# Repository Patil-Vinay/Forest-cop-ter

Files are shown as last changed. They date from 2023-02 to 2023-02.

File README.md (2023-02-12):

# Forestcopter

The main objective of creating an application-based drone is to introduce the tech world and tech community to head towards advantageous approach of saving a life with an Unmanned Aerial Vehicles (UAVs), conserve time and a huge involvement of precise automated machines that can be created with the fundamental knowledge of computer science, electrical/electronic, and mechanics.

Deployed a drone into the forest sector so that it can come handy for the Forest Rescue Department. Thus following were the features that were customized into it:

- Camera Surveillance using Raspberry Pi
- Calling system using GSM Module
- Forest Fire prediction system
- GPS Location
- First Aid Box that opens through servo motor
- All these applications could be observed or controlled through GUI APP.

## Graphical Abstract
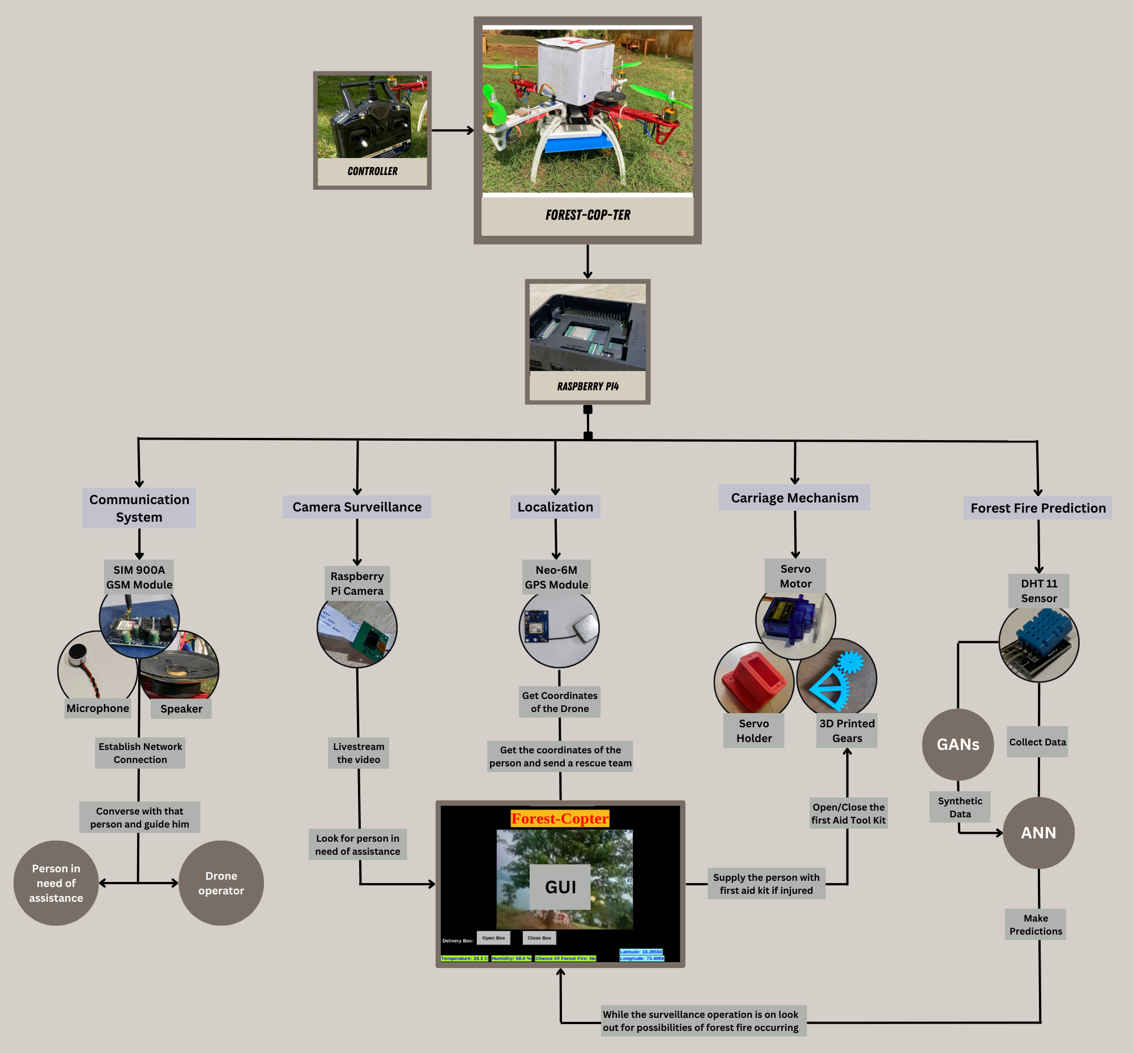
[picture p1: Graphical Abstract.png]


## Project Preview
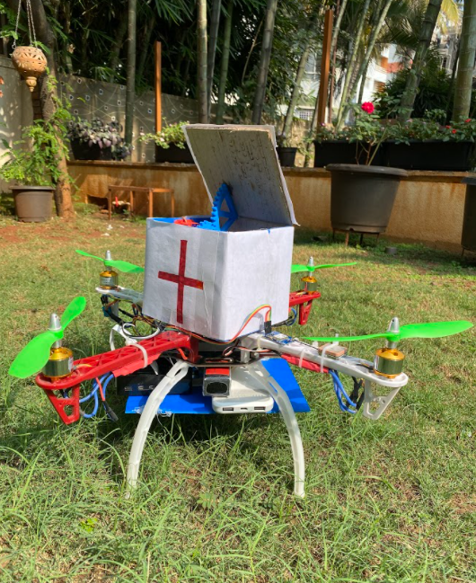
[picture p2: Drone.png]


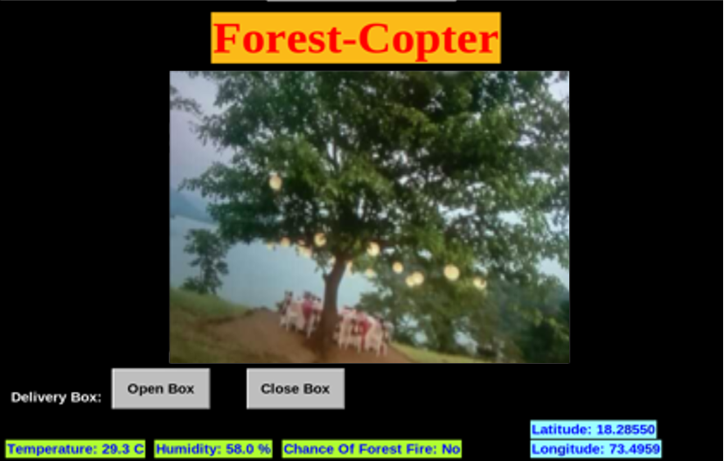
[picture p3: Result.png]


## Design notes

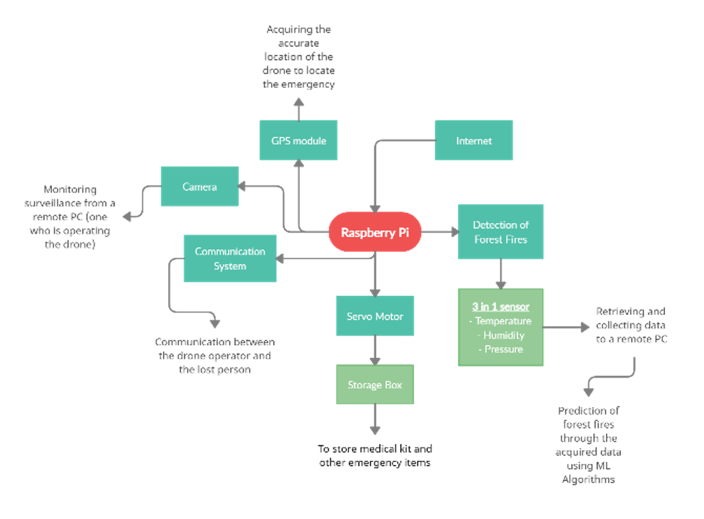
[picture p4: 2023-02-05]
Block Diagram.png

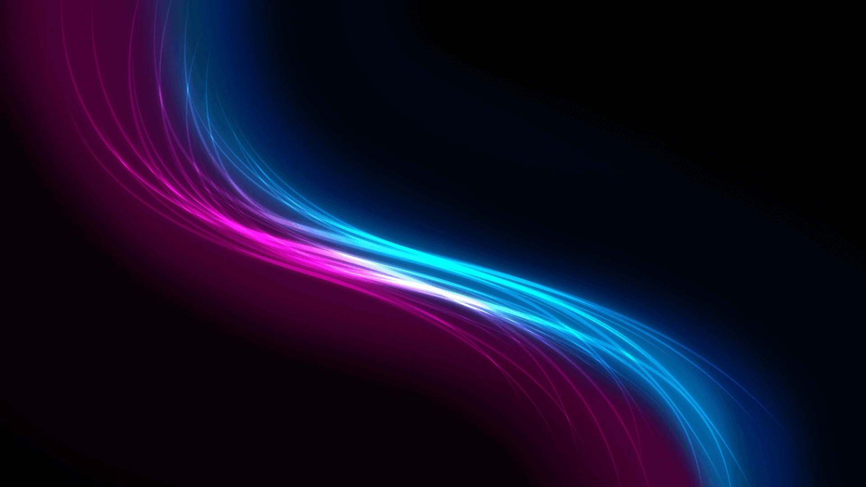
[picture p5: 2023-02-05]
bg.gif

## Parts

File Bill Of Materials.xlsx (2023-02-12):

Designator | Component | Number | Cost per unit - USD | Total cost - USD | Source of materials | Material type
P01 | RaspberryPi 4 | 1 | 70 | 70 | https://robu.in/ (https://robu.in/product/raspberry-pi-4-model-b-with-4-gb-ram/) | Semiconductor
P02 | Orange 5200mAh Battery | 1 | 42 | 42 | https://robu.in/ (https://robu.in/product/orange-5200mah-3s-40c80c-lithium-polymer-battery-pack-lipo/) | Non-specific
P03 | Neo6m GPS Module | 1 | 3.71 | 3.71 | https://robu.in/ (https://robu.in/product/ublox-neo-6m-gps-module/) | Semiconductor
P04 | RaspberryPi Camera | 1 | 25.44 | 25.44 | https://robu.in/ (https://robu.in/product/raspberry-pi-camera-v2/) | Semiconductor
P05 | GSM Sim900A | 1 | 13.32 | 13.32 | https://www.amazon.in/ (https://www.amazon.in/Electronics-SIM900A-Modem-Antenna-Module/dp/B07145FD3J) | Semiconductor
P06 | TowerPro Micro Servo SG90 | 1 | 1.93 | 1.93 | https://robu.in/ | Polymer
P07 | DHT11 Temperature Sensor | 1 | 1.2 | 1.2 | https://robu.in/ (https://robu.in/product/dht11-temperature-and-humidity-sensor-module-with-led/) | Semiconductor
P08 | Microphone | 1 | 0.59 | 0.59 | https://robu.in/ (https://robu.in/product/microphone-97mm-pack-of-3/) | Semiconductor
P09 | Speaker | 1 | 0.55 | 0.55 | https://www.electronicscomp.com/ (https://www.electronicscomp.com/8-ohm-speaker-0.5-watt) | Semiconductor
P10 | DJI F450 Drone Frame | 1 | 20.84 | 20.84 | https://www.amazon.in/ (https://www.amazon.in/Invento-Quadcopter-MultiCopter-Airframe-Landing/dp/B07D42SS88) | Polymer
P11 | Simonk 30A ESC | 4 | 4.85 | 19.4 | https://robu.in/ (https://robu.in/product/30a-bldc-esc-electronic-speed-controller/) | Semiconductor
P12 | 1000KV Brushless Motor | 4 | 3.64 | 14.56 | https://robu.in/ (https://robu.in/product/a2212-10t-13t-1000kv-brushless-motor-without-soldered-connector/) | Metal
P13 | 8x4.5” Propeller | 4 | 1.2 | 4.8 | https://robu.in/ (https://robu.in/product/orange-hd-propellers-80458x4-5-abs-1cw1ccw-1pair-green/) | Polymer
P14 | KK2.1 Flight Controller | 1 | 50.9 | 50.9 | https://robu.in/ (https://robu.in/product/kk2-1-5-multi-rotor-lcd-flight-control-board-with-6050mpu-and-atmel-644pa/) | Semiconductor
P15 | Flysky 6CH Controller | 1 | 30.28 | 30.28 | https://robu.in/ (https://robu.in/product/ct6b-flysky-2-4ghz-6ch-transmitter-wfs-r6b-receiver-mode-2/) | Semiconductor
P16 | PLA | 1 | 9.69 | 9.69 | https://robu.in/ (https://robu.in/product/orange-epla-1-75mm-3d-printing-filament-1kg-white/) | Polymer
P17 | USB to Type C cable | 1 | 1.72 | 1.72 | https://robu.in/ (https://robu.in/product/5v-3a-usb-to-type-c-cable-with-on-off-switch-power-control-for-raspberry-pi-4b-1-meters-black/) | Non-specific
P18 | Dual USB Output | 1 | 2.42 | 2.42 | https://robu.in/ (https://robu.in/product/dual-usb-output-9v-12v-24v-36v-car-charger-switch-5v-dc-dc-power-supply-module-3a-buck-regulator/) | Semiconductor
P19 | Pole Wire Connector Terminal Block | 1 | 1.56 | 1.56 | https://robu.in/ (https://robu.in/product/pct-spl-62-0-08-2-5mm-62-pole-wire-connector-terminal-block-with-spring-lock-lever-for-cable-connection/) | Semiconductor
P20 | Jumper Wires | 1 | 1.09 | 1.09 | https://robu.in/ | Semiconductor
P21 | Small Breadboard | 1 | 0.35 | 0.35 | https://robu.in/ (https://robu.in/product/170-pts-mini-breadboard-syb-170-white/) | Semiconductor
P22 | Cardboard | 1 | 0.61 | 0.61 | Local Store | Non-specific
P23 | Sheet metal | 1 | 1.21 | 1.21 | Local Store | Metal
P24 | Spacers | 1 | 0.12 | 0.12 | Local Store | Polymer

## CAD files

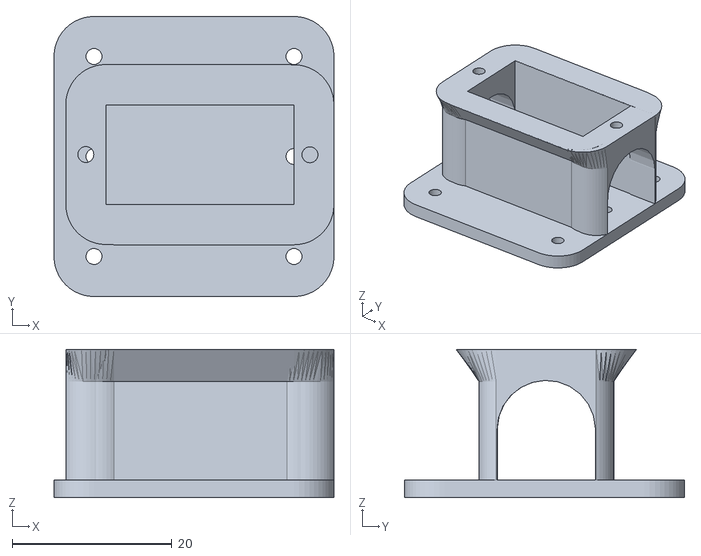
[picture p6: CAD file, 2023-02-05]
Servo_Holder.stl
35.0 x 35.0 x 18.5

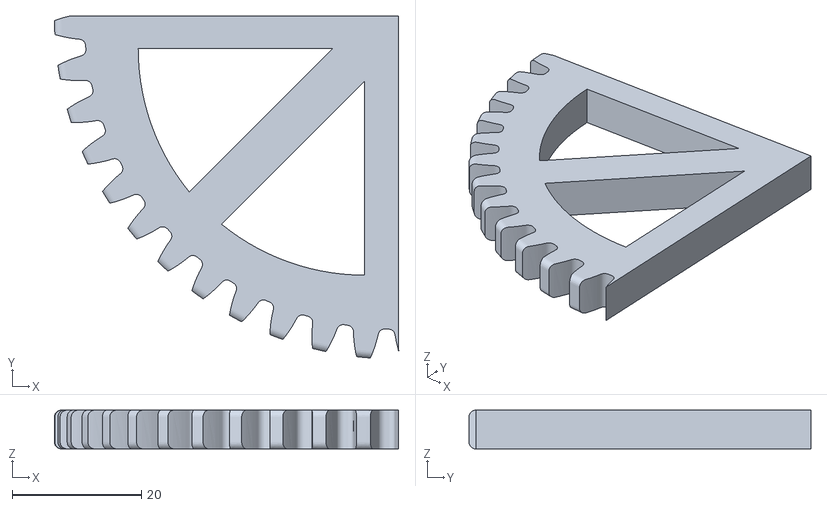
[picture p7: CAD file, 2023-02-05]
gear_mech_mount.stl
53.2 x 52.9 x 6.00

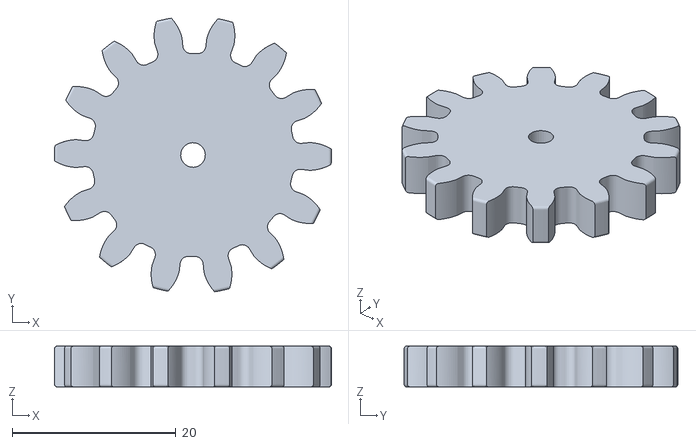
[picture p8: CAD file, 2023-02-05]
gear_mechanism.stl
33.8 x 33.4 x 5.00

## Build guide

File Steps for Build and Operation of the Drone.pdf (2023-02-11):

Steps for Build and Operation of the Drone:

A) Drone Assembly:
1. Mount 1000KV Brushless motors to the F450 quadcopter frame using M3 screws.
2. Solder the ESC and power wire to the power pads and insert the power wire in the Pole Wire Terminal block, making sure to connect blue for positive or negative.
3. Mount the KK2.1 flight controller on the top of the quadcopter frame.
4. Connect the ESCs to the motors and connect the signal cable from the ESCs to the flight controller (white wire is the signal, red is power, and black is ground).
5. Connect the Flysky receiver to the flight controller (signal to signal, +5V to +5V, and ground to ground).
6. Connect the receiver channels to the flight controller, starting with Channel 1 at the topmost pin on the left side.
7. Assemble the top and bottom boards to the arms and legs of the quadcopter frame.
8. Calibrate the Flight controller and ESC.
9. Connect the propellers and test the drone in an open environment.
10. Mount all components, such as the Raspberry Pi, sensors, and carriage mechanism, on the drone.
11. Create a box or make a box from cardboard and cut a sheet metal of 12x12cm dimension and fix it with the base of the box.
12. Attach the box to the top plate of the drone with spacers.
B) Interfacing Raspberry Pi with required components:
1. Connect the Pole Wire Terminal block output to the input of the Dual USB Output module.
2. Use a USB to type C cable to connect the Dual USB Output module to the USB port of the Raspberry Pi 4 to power it.
3. Connect the Raspberry Pi camera to the camera module port of the Raspberry Pi 4.
4. Connect the Vcc pin of the Neo6M GPS module to 5V of the Raspberry Pi 4, the Ground pin of the GPS module to Ground of the Raspberry Pi 4, and the Tx pin of the GPS module to the Rx pin (GPIO 27) of the Raspberry Pi 4.
5. Connect the Vcc pin of the DHT11 Temperature sensor to 3.3V of the Raspberry Pi 4, the Ground pin of the Temperature sensor to Ground of the Raspberry Pi 4, and the data pin of the temperature sensor to GPIO 4 of the Raspberry Pi 4.
6. Connect the Vcc pin of the TowerPro Micro Servo SG90 Motor to 5V of the Raspberry Pi 4, the Ground pin of the servo motor to Ground of the Raspberry Pi 4, and the signal pin of the servo motor to GPIO 18 of the Raspberry Pi 4.
7. Connect the Vcc pin of the GSMSim900A module to 5V of the Raspberry Pi 4, the Ground pin of the GSM module to Ground of the Raspberry Pi 4, and the Rx pin of the GSM module to the Tx pin (GPIO 14) of the Raspberry Pi 4 and the Tx pins of the GSM module to the Rx pin (GPIO 15) of the Raspberry Pi 4.
8. Connect the microphone and speaker to the ports on the GSM module, with the positive wire of the microphone connecting to the "mic_p" port and the negative wire connecting to the "mic_n" port, and the positive wire of the speaker connecting to the "spk_p" port and the negative wire connecting to the "spk_n" port.

C) Generate networks :
1. Load on your Google Drive the notebook files: SyntheticData.ipynb , forestfire_prediction.py.
2. Load on your Google Drive forestfires.csv dataset to be used with the SyntheticData.ipynb file in order to generate the synthetic data.
3. Open the file SyntheticData.ipynb with Google Colaboratory, choose runtime session from the Menu and execute.
4. Load on your Google Drive the file generated from step 3 or you can load the forestfire_augmented.csv dataset to be used with forestfire_prediction.py to train the ANN model and make predictions.
5. Repeat step 3 with forestfire_prediction.py, the output model files will be saved in the same directory of the notebook file.
D) Flysky Transmitter and Receiver Pairing

If the Flysky receiver LED is blinking, this means that the ESC is not paired with the transmitter. To pair the two devices, follow these steps:

1. Disconnect all connections from the Flysky receiver.
2. Connect one of the ESCs to the receiver.
3. Power the ESCs by connecting the battery (P02) to the power cable of the frame.
4. Connect the ESC cable that will go to the flight controller to Channel 1 (CH1) of the receiver.
5. Short the signal and ground pins of the receiver at the BAT channel. If the receiver is not paired, the LED on the receiver will blink continuously.
6. Set the trim levels of the transmitter to the middle position.
7. Press and hold the bind button on the transmitter while turning it on.
8. Observe the receiver LED. If it stops blinking, this means that the transmitter and receiver are paired.
9. Disconnect the power and turn off the Flysky transmitter.
E) Calibrating the Flight Controller
1. Turn on the Flysky transmitter and power the quadcopter by connecting the battery to the power cable.
2. Press the S4 button to access the menu and select the quadcopter X mode by navigating with S2 and S3 buttons.
3. Calibrate the ACC by placing the drone on a flat surface.
4. Perform a Receiver Test in the menu by using S2 and S4 buttons.
5. Set the PI settings according to the table given below.

Instructions for PI Settings:

Parameter | Roll (Aileron) | Pitch (Elevator) | Yaw (Rudder)
P Gain | 75 | 75 | 75
P Limit | 50 | 50 | 20
I Gain | 40 | 40 | 30

I Limit | 20 | 20 | 10
6. Go to the Mode Settings and set the self-level to always.
7. Go to the Miscellaneous Settings and set the Alarm 1/10 volts to 108. This alarm will sound when the supply voltage drops to 10.8V.
F) ESC Calibration
1. Turn on the Flysky transmitter with the throttle stick at minimum and all switches off.
2. Move the throttle stick to maximum.
3. Press and hold S1 and S4 buttons on the flight controller, then connect the battery.
4. Listen for two beep sounds, then move the throttle stick to minimum and listen for a single beep sound.
5. This will complete the ESC calibration.
6. Arm the quadcopter by moving the throttle stick to the bottom left corner.
7. Increase the throttle to verify that the motors are running. Do not attach the propellers.
8. Check the motor rotation and make sure it follows the X configuration.
9. If the rotation is incorrect, interchange the last two wires of the ESC connected to the motor.
G) Calibrating the Raspberry Pi:
1. Write the Raspberry Pi operating system to an SD card using the Raspberry Pi Imager tool.
2. Insert the SD card into the Raspberry Pi and power it on, then follow the on-screen instructions to set it up.
3. Open the terminal and install the required libraries: tkinter, DHT11, PIL, OpenCV, panda, sklearn, keras, pynmea, and smtplib.
4. To use the internet with a GSM module, disable the serial option and connect the Raspberry Pi to the internet via WiFi or Ethernet. Install the PPP software and create a PPP peer configuration file, changing the APN and communication port as needed.
5. Use soft_uart to convert the GPIO pins into Rx and Tx for serial communication.
6. Test the functionality of each sensor/module before running the final file.
7. Install VNC Server on Raspberry Pi and VNC Viewer on the master computer, then connect to the Raspberry Pi remotely using the IP address.
8. Run the "forest-copter" micro python file to see the GUI with information on temperature, humidity, camera feed, GPS module, and forest fire prediction.

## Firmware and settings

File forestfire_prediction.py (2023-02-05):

import RPi.GPIO as GPIO
import dht11
import time
import pandas as pd
from sklearn.preprocessing import StandardScaler
from keras.models import load_model
import smtplib

# initialize GPIO
GPIO.setwarnings(False)
GPIO.setmode(GPIO.BCM)
GPIO.cleanup()
instance = dht11.DHT11(pin =4)

#features and labels
features = []
labels = []

while True:
    # get sensor data
    result = instance.read()
    if result.is_valid():
        temperature = result.temperature
        humidity = result.humidity
        features.append([temperature, humidity])
        #print("Temperature: %d C" % temperature)
        #print("Humidity: %d %%" % humidity)
    else:
        print("Error: %d" % result.error_code)
        
    # preprocessing
    X, Y = features,labels
    sc_features = StandardScaler()
    X = sc_features.fit_transform(X)
    X = pd.DataFrame(X, columns = features.columns)
    
    # load model
    model = load_model('forest_fire_model.h5')
    
    # make predictions
    predictions = model.predict(X)
    predictions = [1 if x > 0.5 else 0 for x in predictions]
    
    # check for forest fire
    if predictions[-1] == 1:
	prediction = "Yes"
        print("ALERT: Forest fire detected!")
    else:
	prediction = "No"
        print("No forest fire detected.")

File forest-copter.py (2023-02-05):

from tkinter import *
import tkinter as tk
import RPi.GPIO as GPIO
from DHT11_Python import dht11 
import 
import time
import datetime
import threading
import tkinter.font as tkFont
from PIL import ImageTk,Image

import forestfire_prediction
temperature = forestfire_prediction.temperature
humidity= forestfire_prediction.humidity
prediction = forestfire_prediction.prediction

import serial
import time
import string
import pynmea2
import cv2

import picamera
import picamera.array

GPIO.setwarnings(False)
GPIO.setmode(GPIO.BCM)

GPIO.setup(18,GPIO.OUT)
pwm = GPIO.PWM(18,50)
pwm.start(0)

root = tk.Tk()
#image = PhotoImage(file="bg.gif")
#background=Label(root, image=image)
root.geometry("1280x720") #You want the size of the app to be 500x500
root.resizable(0, 0) #Don't allow resizing in the x or y direction

label.grid(row=0, column=0)
cap= cv2.VideoCapture(0)

back = tk.Frame(master=root,bg='black')
back.pack_propagate(0) #Don't allow the widgets inside to determine the frame's width / height
back.pack(fill=tk.BOTH, expand=1) 
# background.place(x=0,y=0,relwidth=1, relheight=1)

title_Label = Label(root, fg="red", background="#FBB917", text="Forest-Copter", font=("Times New Roman", 50,"bold"))
title_Label.place(x = 300, y=20)


temperature = StringVar()
temperature.set("----"+" °C")

humidity = StringVar()
humidity.set("----"+" %")

prediction= StringVar()
prediction.set("----")

lat = StringVar()
lat.set("----")

lng = StringVar()
lng.set("----")

def Open():
    duty = 2
    while duty <= 10:
        pwm.ChangeDutyCycle(duty)
        time.sleep(0)
        duty = duty +1
        
def Close():
    pwm.ChangeDutyCycle(2)
    time.sleep(0.5)
    pwm.ChangeDutyCycle(0)

temperatureLabel = Label(root, fg="blue", background="#ADFF2F", textvariable=temperature, font=("Arial", 15,"bold"))
temperatureLabel.place(x = 10, y = 680)

humidityLabel = Label(root, fg="blue", background="#ADFF2F", textvariable=humidity, font=("Arial", 15,"bold"))
humidityLabel.place(x = 220, y = 680)

predictionLabel = Label(root, fg="blue", background="#ADFF2F", text="Chance Of Forest Fire: ", font=("Arial", 15,"bold"))
predictionLabel.place(x = 400, y = 680)

predictionLabel = Label(root, fg="blue", background="#ADFF2F", textvariable=prediction, font=("Arial", 15,"bold"))
predictionLabel.place(x = 430, y = 680)

gps_latitude = Label(root, fg="blue", background="#9AFEFF", textvariable=lat , font=("Arial", 15,"bold"))
gps_latitude.place(x = 750, y = 650)

gps_longitude = Label(root, fg="blue", background="#9AFEFF", textvariable=lng, font=("Arial", 15,"bold"))
gps_longitude.place(x = 750, y = 680)

DeliveryLabel = Label(root, fg="white",background ="#000000",text=" Delivery Box: ", font=("Arial", 15,"bold"))
DeliveryLabel.place(x = 10, y = 600)

motorOpenButton = Button(root,fg="black",background="#C0C0C0", text="Open Box", font=("Arial", 15,"bold"), height = 2, width = 10, command=Open)
motorOpenButton.place(x=160 ,y=570)

motorCloseButton = Button(root,fg="black",background="#C0C0C0", text="Close Box", font=("Arial", 15,"bold"), height = 2, width = 10, command=Close)
motorCloseButton.place(x=350 ,y=570)

root.attributes("-fullscreen",True)
root.bind("<e>",exit)

def exit():
    root.quit()

    
def gpssensor():
    root.after(6000, gpssensor)
    while True:
        port="/dev/ttyAMA0"
        ser=serial.Serial(port, baudrate=9600, timeout=0.5)
        dataout = pynmea2.NMEAStreamReader()
        newdata=ser.readline()

        if newdata[0:6] == "$GPRMC":
            newmsg=pynmea2.parse(newdata)
            lat=newmsg.latitude
            lng=newmsg.longitude
            gps = "Latitude=" + str(lat) + "and Longitude=" + str(lng)

def show_frames():
   root.after(6000, gpssensor)
   cv2image= cv2.cvtColor(cap.read()[1],cv2.COLOR_BGR2RGB)
   img = Image.fromarray(cv2image)
   imgtk = ImageTk.PhotoImage(image = img)
   label.imgtk = imgtk
   label.configure(image=imgtk)
   label.after(20, show_frames)

def read_every_second():
    gpssensor()
    win.after(1000, read_every_second)


read_every_second()
show_frames()
root.mainloop()
